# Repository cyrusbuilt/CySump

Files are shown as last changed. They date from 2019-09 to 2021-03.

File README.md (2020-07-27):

# CySump



ESP8266-based automated IoT sump pump system (Arduino).

The code in this repository represents the Firmware for the CySump IoT sump pump controller device, as well as some components for integrating with [OpenHAB2](https://openhab.org).  CySump is a [PlatformIO](https://platformio.org/) project and is meant to integrate with an existing sump pump and provide 2 things: The ability to detect state (the system's state, pump state, and pit state {water level}) and the ability to control the pump MQTT. Since there is an [ESP8266](https://www.adafruit.com/product/2471) at the heart of it, that means it is WiFi-enabled and is capable of OTA (Over-the-Air) firmware updates.

## Important Note on Security

CySump uses [MQTT](http://mqtt.org/) to pass control messages in JSON format and in turn the device sends status messages in JSON format to MQTT subscribers (such as OpenHAB2). Additionally, these messages are transferred to/from MQTT over TLS using SSL certificates so that the messages are encrypted (when TLS is enabled).  You cannot send control messages to CySump directly. You have to publish them to the control channel on the MQTT broker that CySump is subscribed to. Additionally, you would need the appropriate certificate and SHA256 fingerprint (when TLS is enabled) to connect to and publish the control messages. This security architecture is certainly not infalible, but definitely adds a strong layer of security that was non-existent in previous versions and also provides some means of hardening that security even further (such as using certificates signed by an RSA CA (as opposed to self-signed certs) and using password authentication with the MQTT broker on top of that. You can even configure OpenHAB2 to communicate with the MQTT broker using TLS as well, although this is overkill if the broker is running on the same machine as OpenHAB2 and/or the MQTT standard port is bound to the OpenHAB2 host).

## Theory of Operation

The way this is intended to work is: when the device detects the water level in the pit is at a certain level (at least 40% full by default), it turns on the pump via a relay and when the water level drops back down to at least 5% (by default) it shuts the pump off. If for some reason, the water level reaches roughly 83% full (about 5 inches from the water surface to the top of the pit), then the piezo buzzer will turn on and will not turn back off until the water drops below the alarm threshold. If using the OpenHab2 components, then a push notification will be sent when the water level reaches roughly 80% full and then again if the pit actually floods. The idea is not only to be able to control the pump, but alert the user to critical water level and flood conditions. Ideally, this detection and alert mechanism could be used to minimize or prevent damage.  Water level detection is performed using a special type of capacitive fluid level sensor called an "[eTape](https://www.whiteboxes.ch/shop/etape/)". Since my sump pit is roughly 30", I purchased the 32" (81.28cm) eTape.  There is a library in the [ArduinoHAF](https://platformio.org/lib/show/1185/ArduinoHAF) framework (which is a dependency) called "WaterLevelSensor" which does the heavy lifting. It samples the sensor value, converts to resistance, then converts to percentage
full and fluid depth level.  Previous versions of CySump used an HC-SR04T (and later a JSN-SR04T, which is waterproof) ultrasonic ranging sensor, which sounded like a good idea in theory, but in practice it was just to erratic and unreliable.  The sump pit itself created too much back-scatter for the sensor and on multiple occasions, the water level was higher than reported and the alarm did not sound in time.  The eTape has been ultra-reliable so far, though much more expensive.

## Configuration

The config.h file contains default configuration directives. These options are the hardcoded default values that the system will initially boot with. However, if there is a config.json file present in the root of the SPIFFS file system, then it will override these defaults. Here we'll discuss each option:

- ENABLE_OTA: If you do not wish to support OTA updates, just comment this define.
- ENABLE_MDNS: If you do not wish to support [MDNS](https://tttapa.github.io/ESP8266/Chap08%20-%20mDNS.html), comment this define.
- ENABLE_TLS: If you wish to use TLS support (MQTT-over-SSL), uncomment this define.
- PIT_DEPTH_INCHES: The depth of the pit in inches. Or more importantly, the distance between the sensor and the bottom of the sump pit. Default is 30.
- ALARM_DEPTH_INCES: This is the *remaining* depth to consider the sump pit to be critical. This is the distance (in inches) from the sensor to the water surface. Default is 5 inches (remaining before flooding).
- CONFIG_FILE_PATH: This is the path to the configuration file. The default is /config.json. The values in this file will override these defaults.
- DEFAULT_SSID: Change this line to reflect the SSID of your WiFi network.
- DEFAULT_PASSWORD: Change this line to reflect the password to your WiFi network.
- CLOCK_TIMEZONE: The GMT offset for your timezone (EST [America/New York] is -4 when observing DST. It's -5 when not.)
- SERIAL_BAUD: While it is not recommended, you can change the BAUD rate of the serial port here.
- CHECK_WIFI_INTERVAL: The interval (in milliseconds) to check to make sure the device is still connected to WiFi, and if not attempt to reconnect. Default is 30 seconds.
- CHECK_SENSORS_INTERVAL: The interval (in millisceonds) to check the water depth.
- CLOCK_SYNC_INTERVAL: The interval (in milliseconds) to try to resync the clock with NTP. Default is 1 hour.
- DEVICE_NAME: This essentially serves as the host name of the device on the network.
- CHECK_MQTT_INTERVAL: The interval (in milliseconds) to check connectivity to the MQTT broker. If the connection is lost, a reconnect will occur. The default value is 35 seconds.
- MQTT_TOPIC_STATUS: The MQTT status topic to publish device status messages to. Default is 'cysump/status'.
- MQTT_TOPIC_CONTROL: The MQTT control topic to subscribe to for control messages. Default is 'cysump/control'.
- MQTT_BROKER: The hostname or IP of the MQTT broker.
- MQTT_PORT: The port on the MQTT broker to connect to. The default is 8883 (default port for MQTT over TLS).
- OTA_HOST_PORT: Defines the port to listen for OTA updates on. This option is ignored if ENABLE_OTA is disabled.
- OTA_PASSWORD: The password used to authenticate with the OTA server. This option is ignored if ENABLE_OTA is disabled.
- ip: The default IP address. By default, this devices boots with a static IP configuration. The default IP is 192.168.0.202. You can change that here if you wish.
- gw: The default gateway address. The current default is 192.168.0.1. You can change that here if you wish.
- sm: The subnet mask. By default, it is 255.255.255.0, but you can change that here if need be.

To override the default configuration options, you need to upload a filesystem image containing a file named 'config.json' in the root of the SPIFFS filesystem. The file should like something like this:

```json
{
    "hostname": "CYSUMP",
    "useDHCP": false,
    "ip": "192.168.0.202",
    "gateway": "192.168.0.1",
    "subnetMask": "255.255.255.0",
    "dnsServer": "192.168.0.1",
    "wifiSSID": "your_ssid_here",
    "wifiPassword": "your_password_here",
    "webserverPort": 80,
    "otaPort": 8266,
    "otaPassword": "your_ota_password_here",
    "mqttBroker": "your_mqtt_broker_here",
    "mqttPort": 8883,
    "mqttControlChannel": "cysump/control",
    "mqttStatusChannel": "csump/status",
    "mqttUsername": "your_mqtt_username",
    "mqttPassword": "your_mqtt_password",
    "serverFingerprintPath": "/mqtt.fpn",
    "caCertificatePath": "/ca.crt",
    "pitDepth": 30,
    "activatePercentFull": 65,
    "deactivatePercent": 15
}
```

This configuration file is pretty self explanatory and one is included in the source. The file *MUST* be located in the "data" directory located in the root of the project in order to be picked up by the flash uploader (either via Serial or OTA). Each of the options in the configuration file are self-explanatory and match up with the hard-coded default settings mentioned above. If this file is not present when the firmware boots, a new file will be created and populated with the hardcoded defaults. These defaults can then be changed via the fail-safe menu and saved. You'll notice a couple of additional options in the config.json file not present in config.h. They are as follows:

- mqttUsername: If you have enabled password authentication on your MQTT broker, provide the username here.
- mqttPassword: If you have enabled password authentication on your MQTT broker, provide the password for the username above. If *both* the username and password are provided, then CyGarage will attempt to connect to the broker with the provided credentials; Otherwise, it will attempt to connect without credentials.
- mqttControlChannel: The MQTT control topic to subscribe to in order to receive device commands.
- mqttStatusChannel: The MQTT status topic to publish device status to.
- serverFingerprintPath: The path to the file containing the MQTT broker's SHA256 fingerprint. Default is '/mqtt.fpn'.
- caCertificatePath: The path to the CA certificate that the MQTT broker's certificate was signed with. Default is '/ca.crt'.

If the above values are omitted or invalid, then the system will fail during loadCertificates() and will not be able to connect to MQTT.  However, if ENABLE_TLS is commented out, they will be ignored and the system will attempt to connect to the MQTT broker without TLS.

## Getting Started

After you've configured everything the way you need it (as discussed above), build the firmware by either clicking "Build" in the PlatformIO tasks menu, or by opening a terminal to the project directory and typing:

```bash
> platformio run
```

NOTE: The first time you flash the Huzzah, you need to do so over serial (since the OTA code isn't there yet), but subsequent uploads can be done via OTA if configured properly.

The next thing to do is connect the Huzzah to your computer using an FTDI cable like [this one](https://www.adafruit.com/product/70?gclid=EAIaIQobChMIm7-50ZiZ5AIVlIvICh284QPxEAQYBCABEgJkcPD_BwE) and then configure the port in platformio.ini like so:

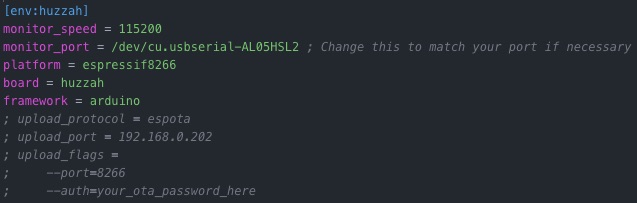
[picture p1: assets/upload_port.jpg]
config


With the above mentioned FTDI cable attached to my MacBook, the port appears as it does in the config file above (usually PlatformIO is pretty good about auto-detecting the port for you).

Now all you have to do is flash the firmware onto the Huzzah. You can do this by first pressing and holding the "GPIO" button and then press the "reset" button and let go of both on the Huzzah to put it into flash mode (this is not necessary when you flash via OTA), then click the "Upload and Monitor" task in the PlatformIO menu or by typing the following into the terminal:

```bash
> platformio run --target upload
> platformio device monitor --baud 115200 --port /dev/cu.usbserial-AL05HSL2
```

Once complete, press the "reset" button on the Huzzah. You should see the device boot up in the serial console. Now put the device back into flash mode. If you are using MQTT over TLS (recommended) then visit the readme in the "openhab" folder (even if you ultimately are not connecting MQTT to OpenHAB) for instructions on generating the necessary files for connecting CySump to MQTT, otherwise just click the "Upload File System Image" task in the PlatformIO menu. When finished, press the "reset" button again and the device will reboot and come back up with your new configuration settings.

## OTA Updates

If you wish to be able to upload firmware updates Over-the-Air, then besides leaving the ENABLE_OTA option uncommented, you will also need to uncomment all the upload_* lines in platformio.ini, and change the line 'upload_port = ' line to reflect the IP of the device and the line '--auth=' to reflect whatever OTA_PASSWORD is set to. Then when you click "upload" from the PlatformIO tasks (or if you execute 'platformio run --target upload' from the command line) it should upload directly over WiFi and once completed, the device will automatically flash itself and reboot with the new version. If you wish to upload a new configuration file, you can also do this via OTA. Assuming the above-mentioned settings are configured, you can then click "Upload File System Image" from the PlatformIO project tasks.

## Serial Console Menu

If the device ever fails to connect to WiFi or if you press the 'I' key on your keyboard while in the serial console, normal operation of the device is suspended and the device will fall into a 'fail-safe' mode and present the user with a command menu. Here we will discuss those menu options:

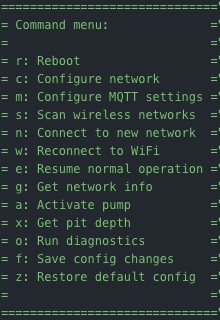
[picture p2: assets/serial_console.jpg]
Console Menu


- Activate Pump - Press 'a'. Activates the pump and ignores inputs until the user stops the pump.
- Reboot - Press 'r'. Self-explanatory. Reboots the device.
- Configure pit depth - Press 'l'. Configure the depth of the sump pit.
- Configure network - Press 'c'. Configure the network.

- - Press 'd' for DHCP or 't' for static IP.

- - If static, then you will also be prompted for the IP, gateway, DNS, and subnet mask.

- Configure MQTT settings - press 'm'. You will be prompted for broker hostname/IP and port, control and status topics, and authentication credentials.

- Scan wireless networks - Press 's'. This will scan for available wireless networks and dump a table of the networks it found to the console.

- Connect to new network - Press 'n'. This option prompts the user for a new SSID and password for different WiFi network to connect to.

- Reconnect to WiFi - Press 'w'. This can be used to reconnect to the current WiFi network if the connection was lost.

- Resume normal operation - Press 'e'. This will leave fail-safe mode and attempt to resume normal operation by resuming any suspended tasks and verify network connectivity.

- Get network info - Press 'g'. This will dump network information to the serial console (IP config, WiFi connection info).

- Run diagnostics - Press 'o'. This will run system diagnostics (similar to POST) to verify critifcal system functions are working correctly.

- Report pit depth - Press 'x'. This lets you get the current depth reading (without triggering any alarm states). Useful for determining the actual depth for configuration.

- Enable alarm - Press 'q'. This enables the audible alarm if disabled.

- Disable alarm - Press 'u'. This disables the audible alarm until manually enabled again.

- Save config changes - Press 'f'. This will save any configuration changes currently stored in memory to config.json.

- Restore default config - Press 'z'. This will restore the firmware configuration back to the factory default settings (the hard-coded defaults). It does this by simply deleting the existing config.json file from flash storage and then immediately rebooting the firmware. Upon reboot, a new config.json file is created and populated with the default settings which are then applied to the running configuration in memory.

## Dependencies

The firmware dependencies will be installed automatically at compile-time.  However, if you wish to install dependencies prior to compiling (for intellisense or to clear warnings/errors in the VSCode editor) you can run the following command:

```bash
> platformio lib install
```

Then go to the platformio menu and click "Rebuild IntelliSense index".

## Tools

Included with this firmware is a few handy tools:

- /disassemble.sh - Disassembles the compiled firmware into a plain text file called 'disassembly.txt'. If the firmware has not been built, it will be compiled first, then disassembled. The disassembly output contains the assembly code, C++ calls, and instruction addresses useful for debugging the executing code or determining the cause of crashes at addresses reported by ESPCrashMonitor during boot.

- tools/clear_flash.sh - Completely clears the flash memory on the ESP8266 of all data (including firmware).

- tools/serial_monitor.sh - Just runs the serial monitor. Pretty much the same as clicking 'Monitor' in the platformio menu, but uses its own settings instead of those found in platformio.ini.

- tools/generate_mqtt_certs.sh - Generates the necessary certificates for the MQTT broker and CySump to communicate over TLS.

## Integration with sump pump

Once the board is assembled (either by having the board etched or by just soldering the necessary components to perf board and making the connections manually), you will need to mount the board somewhere and then make the necessary connections to the pump. To do this involves working with high-voltage. *BE CAREFUL DAMNIT*. I am not liable if you do something wrong and injure yourself or blow up your pump. Ok?? Are we clear on this??

Good. I hope so.

For those of you that have done this sort of thing before, this should be trivial. If you don't have any experience with this stuff, please consider having an electrician do the work or at least someone with experience.  The best approach is *NOT* to modify the power cord on your pump. My best recommendation would be to use a 3-pronged extension cord, cut it in half and then splice the ground and neutral wires back together but leave at lest a few inches of wire out of the outer sheath. When you splice those wires, use something heavy duty (good wire nuts, solder and shrink tube, or maybe good crimp-on connectors rated for high voltage. But don't be silly and just twist them together and wrap them in electrical tape. That's just begging for trouble.

Strip both pieces of remaining 'hot' wire. Connect the 'hot' wire from the male plug to the center terminal of a 3-position toggle switch rated for at least 120VAC @ 10A. Connect the 'hot' wire of the female plug to the NO terminal on the relay. Take another wire of the same guage and connect one end to the NO terminal as well. Take the other end and connect it to one of the other terminals on the toggle switch. When the switch is in the center position, the pump is 'off' and will NOT run. When switched to whatever position that other terminal is, it will be 'manually on'. Now take another wire of the same guage and connect one end to the oposite terminal on the toggle switch and then the other end to the COM terminal on the relay. When switch to this position, the pump will be 'auto', meaning it is controlled by CySump. Ideally, all the switch and wiring will be inside of a proper electrical box with a face plate the switch mounts to. Now connect the male plug to the electrical outlet, and plug the pump into the female end. Test 'manual' mode to verify the pump turns on and nothing bad happens. DO NOT let the pump run for more than a few seconds if there is no water in the pit. You can burn out your pump.

Now you need to mount the eTape sensor. How you do this is up to you and depends on the sump pit. You *should* have a lid on the pit. The eTape should be mounted so that the top of tape is as close to the top of the pit as possible it is generally attached to the wall of the sump pit.  As the fluid level rises, the capacitance value changes. It would be worth checking pit depth from the serial console menu ('x' command) once the sensor is mounted and the pit is completely dry. This would give you a definitive baseline depth reading, not just of the depth of the pit, but more importantly, the distance from where the sensor is mounted, to the bottom of the pit. Even though the standard depth is 30 inches, usually there is some gravel or something like that at the bottom and you also have to consider exactly where the sensor is mounted, all of which affect the depth reading. Adjust the value for PIT_DEPTH_INCHES in config.h to reflect that value.  Sensor position is important!! You may need to take several readings with and without water to get a good baseline.

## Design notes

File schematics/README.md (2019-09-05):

# CySump Schematics

All files were produced using [Fritzing](https://fritzing.org/home/). The following is a list of files and what they are:

- CySump_bb.pdf - A PDF version of the breadboard view.

- CySump_bom.html - The bill of materials in HTML format.

- CySump_pcb.pdf - A PDF version of the PCB view.

- CySump_schem.pdf - A PDF version of the schematic view.

- CySump.fzz - The original Fritzing CAD file.

## NOTES

Firstly, the buzzer and the HCSR04 sensor should *NOT* be mounted to the board. Instead, pin headers should be soldered in there place and then female pin connectors should be used to connect them to the board. This may require making a cable (of sorts) for them and then the buzzer can be mounted somewhere inside whatever housing you use or somewhere external to the board. The sensor needs to be mounted somewhere at the top of the pit. Either by affixing the sensor to a bracket or board that straddles the top of the pit or affixed to the underside of the pit lid, then a cable will need to connect the sensor to the board.

The [Adafruit Power Relay FeatherWing](https://www.adafruit.com/product/3191?gclid=EAIaIQobChMIyfvxycGo4wIVTfDACh0WFg4LEAAYASAAEgL4v_D_BwE) was used because it had a 3V trigger and built-in logic-level and protection circuitry (which means no problems connecting to the ESP8266 and no additional transistors or diodes needed). This board needs to have a pin configured as the 'signal' (trigger) line. I chose pin A which is to the immediate right of the GND pin. This is done by simply soldering the jumper pads next to that pin on the underside of the board.

The power supply used is a 5VDC 1A supply which connects to J2.

NO and COM on the relay should connect to the power line that feeds the pump. This may require cutting and splicing the power cord or modifying an extension cord (the preferred option) and then plugging the pump into the extension. The idea is to use the relay as a power switch. So you want to cut and strip the "hot" wire and connect the 2 ends to the relay.  An even better implementation would be to use a 3-position DPDT Toggle switch rated for at least 120V @ 10A between the power cord and relay. When wired properly, this would allow you to switch between "manual" mode where the pump just runs when needed (or switches over to the float switch that goes with it) and "auto" mode, where CySump then controls the pump in an automated fashion. Personally, I intend to mount an electrical box with a cover plate and toggle switch near the electrical outlet the pump currently plugs into, then cut an extension cord and wire to the switch and CySump controller, with the female end of the extension hanging out so that I can plug the pump into it.

Additionally, I opted to use stacking headers where the pins of the ESP8266 should go (creating a "socket" of sorts) to allow the module to be removable. This is optional, but handy in the event that the module ever becomes damaged or if the EEPROM wears out, or something of that nature, it can be easily replaced.

Lastly, the HCSR04 sensor is NOT waterproof. This presents a problem which I will likely later be resolved with a different sensor. While, I can take some level of precautions by coating most of the module in hot glue or something like that, you cannot cover the cans as they were designed to operate in dry air with nothing in between them. Considering this sensor will be mounted at the top of the pit somewhere or even affixed to the underside of the sump pit lid, sooner or later the moist air will corrode the sensor. As such, the sensor will likely need to be replaced every so often. Since they are cheap ($4 or $5 USD), this isn't an expensive proposition, but should be resolved nonetheless. A future revision will replace this sensor with something more robust and less affected by environmental conditions.

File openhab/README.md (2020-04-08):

# OpenHAB Components

This directory contains components for integrating with OpenHAB2.

## Instructions for integrating with OpenHAB2

The first thing you will need to do if you haven't already, is install an MQTT broker. For the purposes of this guide, I will assume you will be using [Mosquitto](https://mosquitto.org/) and will be installing it on the same machine as OpenHAB2.

To install mosquitto, follow the download and install instructions [here](https://mosquitto.org/download/). But assuming you are installing on an Ubuntu or Ubuntu-based system just run:

```bash
> sudo apt-add-repository ppa:mosquitto-dev/mosquitto-ppa
> sudo apt-get update
> sudo apt install mosquitto mosquitto-clients
```

## The following instructions are only necessary when TLS is enabled

Next we need to generate the necessary SSL certificates that will be used for communication over TLS.  There is a shell script in the tools directory that simplifies this process. Just run:

```bash
> tools/./generate_mqtt_certs.sh
```

You will first be prompted for the hostname and IP address of your MQTT broker (in this example, it is the same as the your OpenHAB2 server). It will also prompt you for some additional information such as country, state/province, Organizational Unit, org name, etc. It will also prompt you for a password. Make note of this password. When the script is finished it will output a bunch of files in tools/certs. As the script indicates, the ones we are most interested in are host_name.key.pem, hostname_.crt.pem, and ca.crt.pem (where host_name is the host name you provided when the tool first ran). These 3 files need to be copied somewhere on your MQTT server. For this example let's assume /etc/mosquitto/certs.

```bash
> sudo mkdir /etc/mosquitto/certs
> sudo cp -f tools/certs/host_name.key.pem /etc/mosquitto/certs
> sudo cp -f tools/certs/host_name.crt.pem /etc/mosquitto/certs
> sudo cp -f tools/certs/ca.crt.pem /etc/mosquitto/certs
```

## END TLS-SPECIFIC CONFIG

Next, we need to configure it.

```bash
> sudo nano /etc/mosquitto/mosquitto.conf
```

First make sure the following line is present:

```txt
listener 1883 localhost
```

This binds port 1883 (the default non-SSL port) for MQTT to only allow traffic from the local host.  This is done because encrypting the traffic between OH2 and MQTT when they are running on the same host is overkill, but we also need to make sure that *ONLY* the localhost can do this.  All other traffic will then have to go through another port. In our case, 'all other traffic' will be encrypted traffic when TLS is enabled. This means we need to define another port and supply the certificates like so:

```txt
listener 1883 localhost

listener 8883
cafile /etc/mosquitto/certs/ca.crt.pem
certfile /etc/mosquitto/certs/host_name.crt.pem
keyfile /etc/mosquitto/certs/host_name.key.pem
```

If you are *NOT* using TLS, you can simply leave all the certificate lines out of the config (or comment them). Now press CTRL+X to save and close the file.  Now restart MQTT:

```bash
> sudo systemctl restart mosquitto.service
> sudo systemctl status mosquitto.service
```

It should start back up normally and show the status as active. Now lets test it out:

```bash
> mosquitto_sub -h localhost -p 1883 -t cysump/status &
> mosquitto_pub -h localhost -p 1883 -t cysump/status -m "{\"foo\":\"bar\"}"
{"foo":"bar"}
```

You should see the message output. Now you can kill the subscription you created with the first command:

```bash
> fg
```

Now press CTRL+C.

Next, we need to configure OpenHAB to use the MQTT broker. To do this, go to PaperUI -> Addons -> Bindings and install the MQTT Binding.  Once the installation is complete, we need to configure the service:

```bash
> sudo nano /etc/openhab2/services/mqtt.cfg
```

Add the following lines:

```txt
mqtt:localBroker.url=tcp://localhost:1883
mqtt:localBroker.clientId=openhab2
mqtt:localBroker.qos=0
```

Save and close the file.

## Optional password authentication

If you wish to use password authentication with Mosquitto, then there are some additional steps. First, you need to generate the password file.

```bash
> sudo mosquitto_passwd -c /etc/mosquitto/passwd cysump
```

Where "cysump" is the username. You can make this whatever you want as long as this same username is what you put in the CySump config and in the mqttbridge.things file (if you don't already have an existing bridge). Next, we need to modify the mosquitto config again:

```bash
> sudo nano /etc/mosquitto/mosquitto.conf
```

And add the following lines to the file:

```txt
allow_anonymous false
password_file /etc/mosquitto/passwd
```

Save and close, then restart the service:

```bash
> sudo systemctl restart mosquitto.service
```

Next we need to copy the following files to the openhab-conf folder on the server:

## rrd4j.persist

This is a persistence configuration file. This is only needed if you are using RRD4J for the persistence engine in OpenHAB2 and don't already have a persistence file for it (althouh the settings in this file are recommended). NOTE: Peristence is required to make use of historical water depth tracking. If you don't need this feature or are using a different persistence engine, you can ignore this file. Otherwise, copy this file to the openhab-conf/persist directory.

## mqttbridge.things

This is a "Thing" definition for the MQTT bridge. This bridge can be used by anything else in OH2 that needs it. This simply defines a bridge to MQTT that registers OH2 as a client. If a Thing definition for this bridge already exists, no need to copy it again. If not, then copy this file to the openhab-conf/things directory.

## cysump.things

This is a "Thing" definition for CySump that binds the channels we need to MQTT.  You can edit the binding if needed, (such as adding the mosquitto username and password, hostname or IP and port) then copy this file to the openhab-conf/things directory.

## cysump.items

This file defines the items that will bind to the channels in the cysump.things file, which will represent controls and display values. Copy this file to your openhab-conf/items folder.

## cysump.sitemap

This is the sitemap contains all the items defined in the cysump.items file and makes up all the monitor and control items on one screen. Copy this file to your openhab-conf/sitemaps folder.

## cysump.rules

Contains automation logic. This file is responsible for sending push notifications if the pit is getting too full or if it has flooded, and handles the control actions. Copy this file to your openhab-conf/rules folder.

## All set

Now that everything is in place. You need to restart OH2:

```bash
> sudo systemctl restart openhab2.service
```

Now lets make sure the service started successfully:

```bash
> sudo systemctl status openhab2.service
```

The service should be active. So let's test it:

```bash
> mosquitto_pub -h localhost -p 1883 -t cysump/status -m "{\"client_id\":\"test\",\"pumpState\":\"OFF\",\"firmwareVersion\":\"1.0\",\"systemState\":0,\"waterLevelPercent\":50,\"waterDepth\":12,\"pitState\":\"LOW\",\"alarmEnabled\":true}"
```

Now if you navigate to BasicUI in OH2 and click the CySump sitemap, you should see the System ID is "test", Firmware version is "1.0", System State is "Booting 0" and Pump state is "OFF".

CySump Sitemap (Web Version)

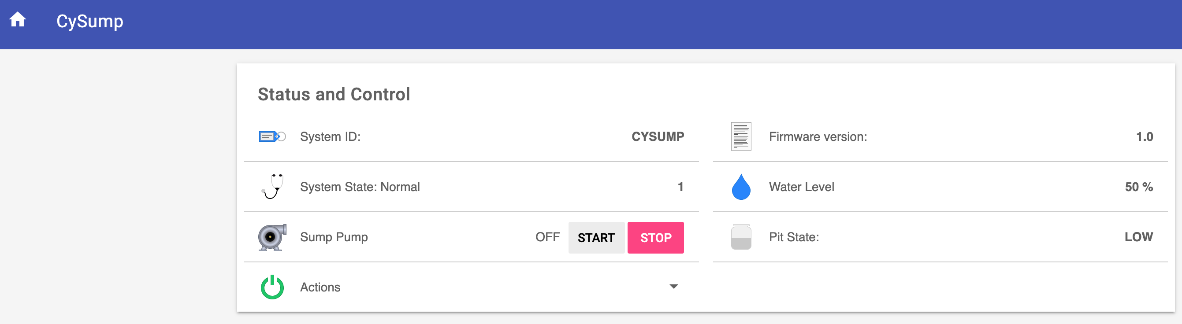
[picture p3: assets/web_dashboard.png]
Web Dashboard


CySump Sitemap (OH2 Mobile App Version)

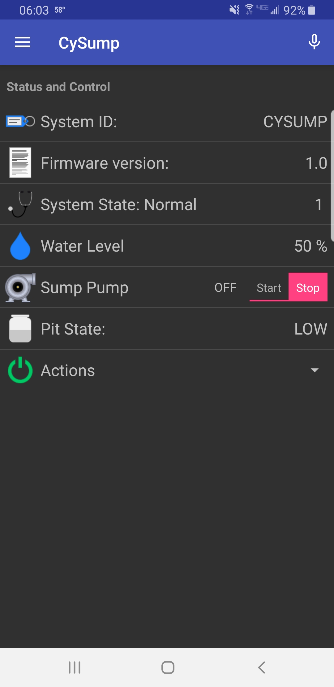
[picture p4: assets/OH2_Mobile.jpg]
Mobile Dashboard


## Dependencies

You will need the following dependent add-ons installed in OpenHAB2 for these components to work correctly:

[openHAB Cloud Connector](https://www.openhab.org/addons/integrations/openhabcloud/)

- You also need to connect your local OpenHAB server to a cloud instance in order to receive push notifications.

This is because cysump.rules makes use of the sendBroadcastNotification() method which assumes you have linked your local OH2 server to a cloud OH2 instance, which can then make use of push notifications. If you do not wish to use push notifications or just don't want to link your local installation to a secure cloud instance, then don't install the cloud connector and comment out the necessary line cysump.rules.

[RRD4J Peristence add-on](https://www.openhab.org/addons/persistence/rrd4j/)

- Required for historical water depth graphs if no other persistence engine is being used.

If all went well, you can now use CySump with your OH2 installation and control and monitor the sump pump (securely) using the OH2 web console or via the OH2 mobile app.

## Finishing up

At this point the only thing left to do if you haven't already is to compile and upload the firmware (if you are happy with the defaults in config.h and your settings in config.json). Next make sure the device is operating normally and you can ping the IP of the device. You can even publish a command to the device to force it to report it's status back:

```bash
> mosquitto_pub -h localhost -p 1883 -t cysump/control -m "{\"client_id\":\"CYSUMP\",\"command\": 4}"
```

The 'data' directory in this project should now contain 3 files: config.json, ca.crt, and mqtt.fpn.

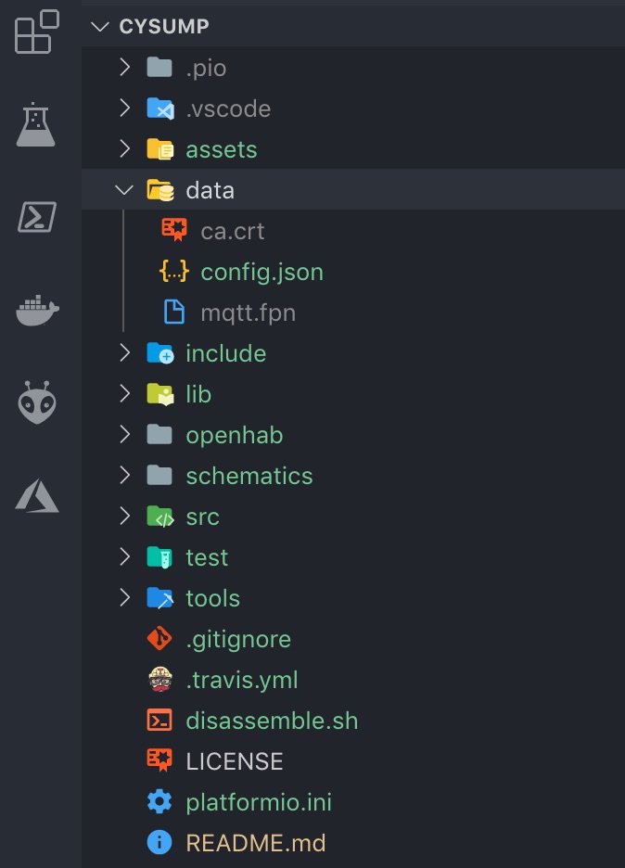
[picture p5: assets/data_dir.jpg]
Data Folder


If so, click "Upload File System image" from the PlatformIO tasks and it will upload those files to CySump and it will reboot when finished. Once it comes back up, it should be able to establish a connection to MQTT and you should see it's status in OH2.

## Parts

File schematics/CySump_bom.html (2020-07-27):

Label | Part Type | Properties
Huzzah ESP8266 | Adafruit HUZZAH ESP8266 | variant variant 2; part # Adafruit #2471
J1 | Piezo Speaker
J2 | Screw terminal - 2 pins | package THT; pins 2; hole size 1.0mm,0.508mm; pin spacing 0.1in (2.54mm)
J3 | Generic male header - 3 pins | row single; package THT; hole size 1.0mm,0.508mm; pins 3; form ♂ (male); pin spacing 0.1in (2.54mm)
LED1 | Green (570nm) LED | package 5 mm [THT]; color Green (570nm); leg yes
LED2 | Red (633nm) LED | package 5 mm [THT]; color Red (633nm); leg yes
LED3 | Yellow (595nm) LED | package 5 mm [THT]; color Yellow (595nm); leg yes
Part1 | Schematic Frame | descr Automated IoT Sump Pump Controller; sheet 1/1; filename CySump.fzz; date 1571939862; project CySump Controller; rev 1.5
Power Relay Featherwing | Adafruit PowerRelay Feather Wing | variant variant 1; part # Adafruit #3191
R1 | 560Ω Resistor | bands 4; package THT; tolerance ±5%; pin spacing 400 mil; resistance 560Ω
S1 | SPST Switch | package switche-dpdt; variant pth2
Amount | Part Type | Properties
1 | Adafruit HUZZAH ESP8266 | variant variant 2; part # Adafruit #2471
1 | Piezo Speaker
1 | Screw terminal - 2 pins | package THT; pins 2; hole size 1.0mm,0.508mm; pin spacing 0.1in (2.54mm)
1 | Generic male header - 3 pins | row single; package THT; hole size 1.0mm,0.508mm; pins 3; form ♂ (male); pin spacing 0.1in (2.54mm)
1 | Green (570nm) LED | package 5 mm [THT]; color Green (570nm); leg yes
1 | Red (633nm) LED | package 5 mm [THT]; color Red (633nm); leg yes
1 | Yellow (595nm) LED | package 5 mm [THT]; color Yellow (595nm); leg yes
1 | Schematic Frame | descr Automated IoT Sump Pump Controller; sheet 1/1; filename CySump.fzz; date 1571939862; project CySump Controller; rev 1.5
1 | Adafruit PowerRelay Feather Wing | variant variant 1; part # Adafruit #3191
1 | 560Ω Resistor | bands 4; package THT; tolerance ±5%; pin spacing 400 mil; resistance 560Ω
1 | SPST Switch | package switche-dpdt; variant pth2

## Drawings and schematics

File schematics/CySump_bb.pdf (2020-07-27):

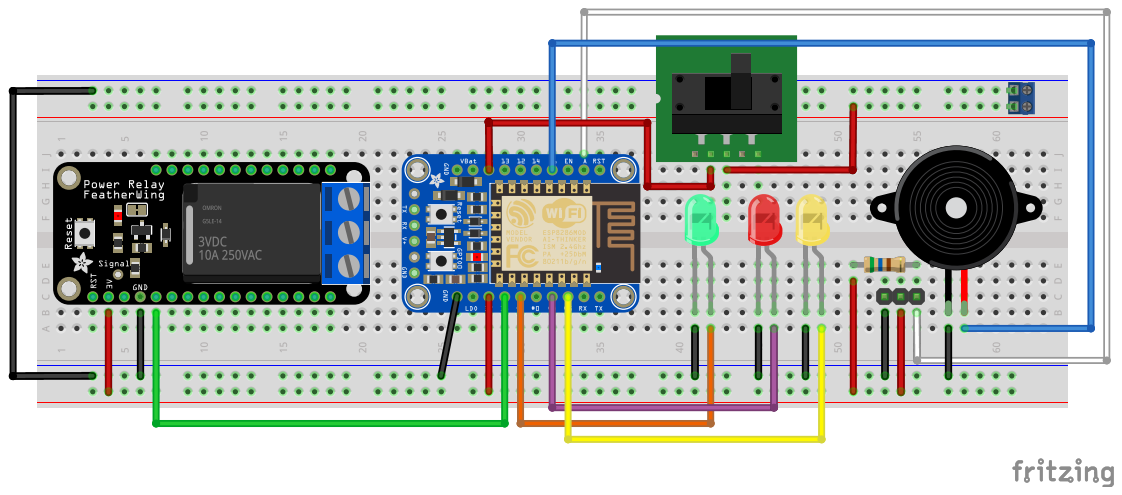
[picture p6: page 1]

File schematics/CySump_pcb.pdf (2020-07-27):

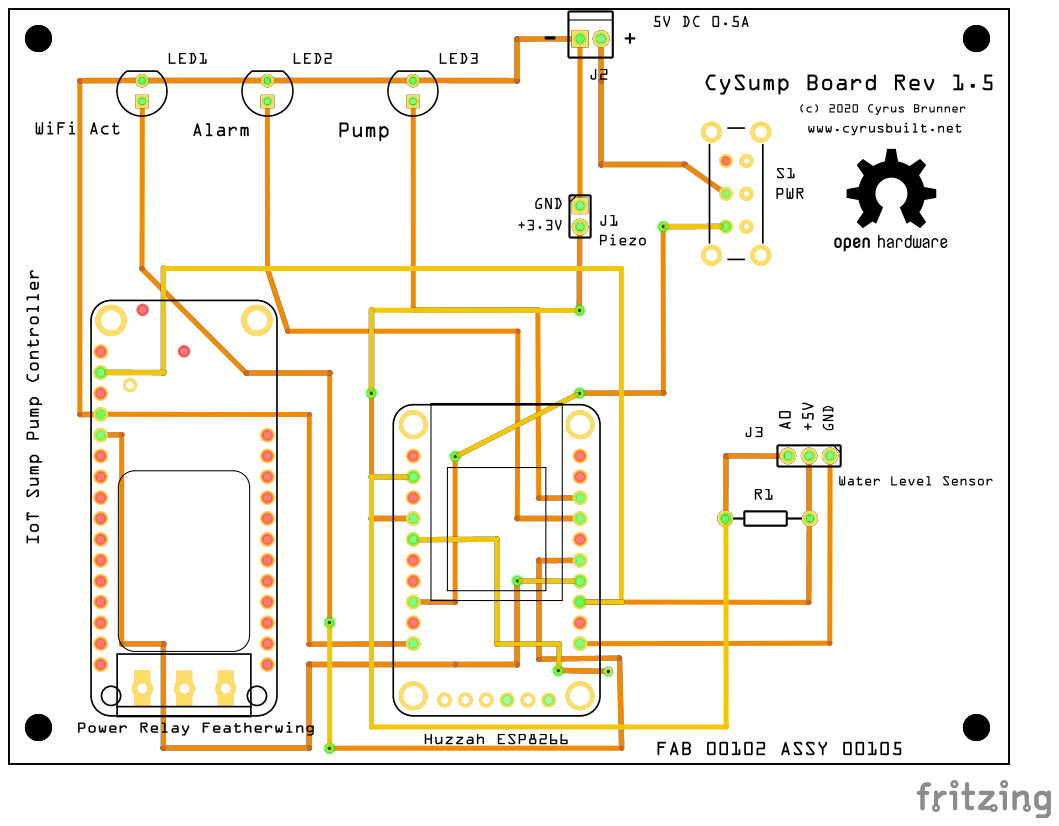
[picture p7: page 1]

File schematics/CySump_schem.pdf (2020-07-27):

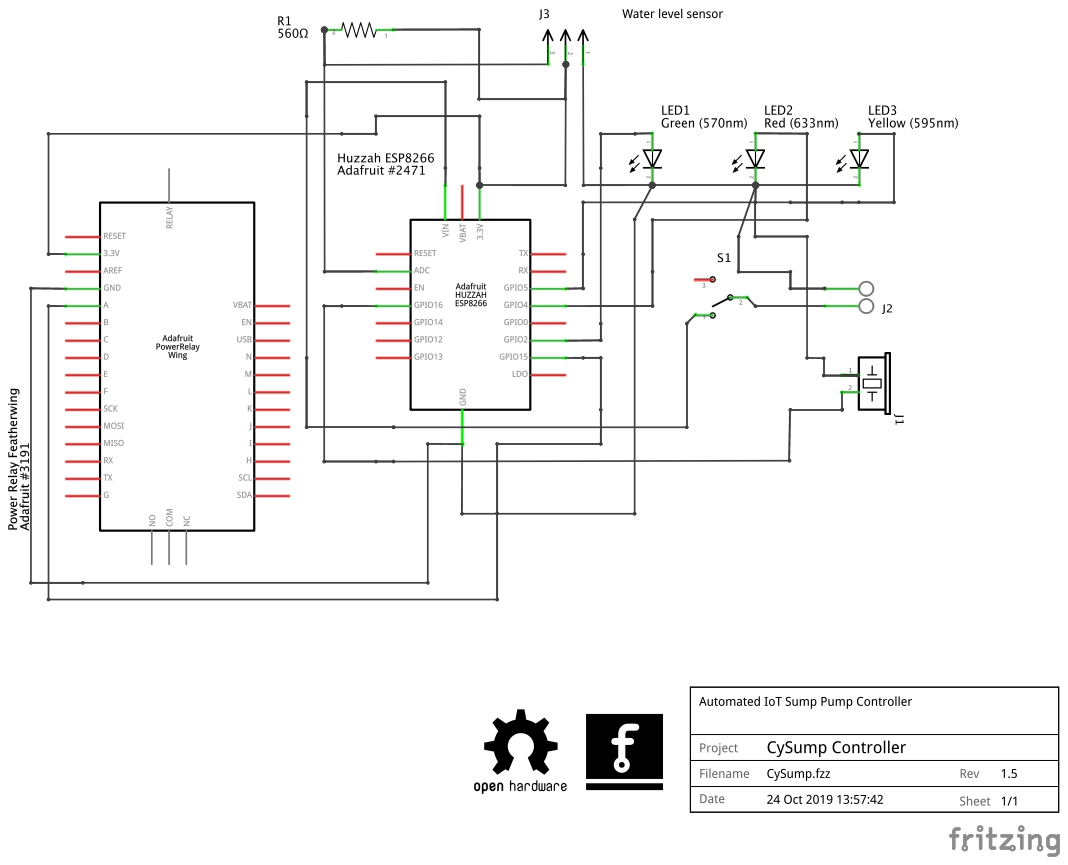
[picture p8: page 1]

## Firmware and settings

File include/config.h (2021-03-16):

/**
 * System Configuration defaults. These values will be used at boot time
 * if no overriding configuration is present.
 */

#ifndef config_h
#define config_h

#include <IPAddress.h>

// Configuration
#define ENABLE_OTA                              // Comment this line to disable OTA updates.
#define ENABLE_MDNS                             // Comment this line to disable the MDNS.
#define PIT_DEPTH_INCHES 32                     // The depth of the sump pit (inches).
#define ALARM_DEPTH_INCHES 5                    // The depth at which to consider an alarm state (inches left until full)
#define CONFIG_FILE_PATH "/config.json"         // The config file path. Do not alter unless you are sure.
#define DEFAULT_SSID "your_ssid_here"           // Put the SSID of your WiFi here.
#define DEFAULT_PASSWORD "your_password_here"   // Put your WiFi password here.
#define CLOCK_TIMEZONE -4                       // The timezone this device is located in. (For example, EST when observing DST = GMT-4, when not = GMT-5)
#define SERIAL_BAUD 115200                      // The BAUD rate (speed) of the serial port (console).
#define CHECK_WIFI_INTERVAL 30000               // How often to check WiFi status (milliseconds).
#define CHECK_SENSORS_INTERVAL 2000             // How often to check sensors (milliseconds).
#define CLOCK_SYNC_INTERVAL 3600000             // How often to sync the local clock with NTP (milliseconds).
#define DEVICE_NAME "CYSUMP"                    // The device name.
#define CHECK_MQTT_INTERVAL 35000               // MQTT connectivity check interval (milliseconds).
#define MQTT_TOPIC_STATUS "cysump/status"       // MQTT status channel to publish to.
#define MQTT_TOPIC_CONTROL "cysump/control"     // MQTT control channel to subscribe to.
#define MQTT_BROKER "your_mqtt_broker_here"     // MQTT broker hostname or IP.
#define MQTT_PORT 8883                          // MQTT port number.
#define DEFAULT_PUMP_ACTIVATE_PERCENT 70        // Default percentage of the sump pit is full before activating the pump.
#define DEFAULT_PUMP_DEACTIVATE_PERCENT 15      // Default percentage of the sump pit is full before deactivating the pump if active.
#ifdef ENABLE_OTA
    #include <ArduinoOTA.h>
    #define OTA_HOST_PORT 8266                     // The OTA updater port.
    #define OTA_PASSWORD "your_ota_password_here"  // The OTA updater password.
#endif
IPAddress defaultIp(192, 168, 0, 202);                 // The default static host IP.
IPAddress defaultGw(192, 168, 0, 1);                   // The default static gateway IP.
IPAddress defaultSm(255, 255, 255, 0);                 // The default static subnet mask.
IPAddress defaultDns(defaultGw);                              // The default static DNS server IP (same as gateway for most residential setups)

typedef struct {
    // Network stuff
    String hostname;
    String ssid;
    String password;
    IPAddress ip;
    IPAddress gw;
    IPAddress sm;
    IPAddress dns;
    bool useDhcp;

    uint8_t clockTimezone;

    // MQTT stuff
    String mqttTopicStatus;
    String mqttTopicControl;
    String mqttBroker;
    String mqttUsername;
    String mqttPassword;
    uint16_t mqttPort;

    // OTA stuff
    uint16_t otaPort;
    String otaPassword;

    // Thresholds
    uint8_t pitDepth;
    uint8_t pumpActivatePercent;
    uint8_t pumpDeactivatePercent;
    uint8_t alarmDepthInches;
} config_t;

#endif

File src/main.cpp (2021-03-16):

/**
 * CySump
 * v1.6
 * 
 * Author:
 *  Cyrus Brunner <cyrusbuilt at gmail dot com>
 * 
 * This is the firmware for the CySump IoT Sump Pump Controller. This firmware
 * specifically targets the Adafruit Huzzah ESP8266, but could easily be
 * adapted to work on any ESP8266 MCU.  It should be relatively easy to adapt
 * to work on ESP32 modules as well, although there would need to be some
 * dependency changes.
 */

// TODO Implement FS checks in self-diags

#ifndef ESP8266
    #error This firmware is only compatible with ESP8266 controllers.
#endif
#include <Arduino.h>
#include <ESP8266WiFi.h>
#include "config.h"
#include <WiFiClient.h>
#include <FS.h>
#include <time.h>
#include "Buzzer.h"
#include "LED.h"
#include "Relay.h"
#include "TaskScheduler.h"
#include "ResetManager.h"
#include "ESPCrashMonitor-master/ESPCrashMonitor.h"
#include "ArduinoJson.h"
#include "ESP8266Ping.h"
#include "PubSubClient.h"
#include "TelemetryHelper.h"
#include "WaterLevelSensor.h"
#include "Console.h"

#define FIRMWARE_VERSION "1.6"

// Pin definitions
#define PIN_WIFI_LED 2
#define PIN_ALARM_LED 4
#define PIN_PUMP_LED 5
#define PIN_RELAY 15
#define PIN_BUZZER 16
#define PIN_LEVEL_SENSOR A0

// Forward declarations
void onRelayStateChange(RelayInfo* sender);
void onCheckWiFi();
void failSafe();
void onCheckMqtt();
void onCheckSensors();
void onMqttMessage(char* topic, byte* payload, unsigned int length);
void onSyncClock();

// Global vars
#ifdef ENABLE_MDNS
    #include <ESP8266mDNS.h>
    MDNSResponder mdns;
#endif
WiFiClient wifiClient;
PubSubClient mqttClient(wifiClient);
WaterLevelSensor sensor(PIN_LEVEL_SENSOR);
Relay pumpRelay(PIN_RELAY, onRelayStateChange, "SUMP_PUMP");
LED alarmLED(PIN_ALARM_LED, NULL);
LED wifiLED(PIN_WIFI_LED, NULL);
LED pumpLED(PIN_PUMP_LED, NULL);
Buzzer alarmBuzzer(PIN_BUZZER, NULL, "AlarmBuzzer");
Task tCheckWifi(CHECK_WIFI_INTERVAL, TASK_FOREVER, &onCheckWiFi);
Task tCheckMqtt(CHECK_MQTT_INTERVAL, TASK_FOREVER, &onCheckMqtt);
Task tSyncClock(CLOCK_SYNC_INTERVAL, TASK_FOREVER, &onSyncClock);
Task tCheckSensors(CHECK_SENSORS_INTERVAL, TASK_FOREVER, &onCheckSensors);
Scheduler taskMan;
config_t config;
float lastDepth = 0;
volatile int percentFull = 0;
bool filesystemMounted = false;
bool manualPumpMode = false;
volatile SystemState sysState = SystemState::BOOTING;
bool alarmDisabled = false;

// TODO Maybe add some logic to measure how fast the water level is rising.
// If rising too fast, especially while the pump is running, this could be
// another alarm condition. Or even more importantly, if the pump is NOT
// running when we expect it to be, that would also be a cause for concern.
// However, I'm not sure how to test that other than to see if the water
// level goes down during pump operation. If it doesn't, then either the
// pump is NOT actually running, or again... the pit is filling faster
// than we can pump. This is a highly unlikely scenario though. You would
// have to have a pretty MAJOR flood problem if the water pump is not able
// to keep up with the incoming water. More than likely, this would simply
// indicate pump failure.


/**
 * Get and print the pump status.
 * @return The pump status ("OFF" or "ON")
 */
String pumpStatus() {
    String state = "OFF";
    if (pumpRelay.isClosed()) {
        state = "ON";
    }

    Serial.print(F("INFO: Pump status = "));
    Serial.println(state);
    return state;
}

/**
 * Gets the pit state based on the specified water level percentage.
 * @param percentFull The percentage of the pit that is full of water.
 * @return 
 */
String pitState(int percentFull) {
    String state = "UNKNOWN";
    if (percentFull == 0) {
        state = "EMPTY";
    }
    else if (percentFull <= 50) {
        state = "LOW";
    }
    else if (percentFull > 50 && percentFull < 75) {
        state = "WARN";
    }
    else if (percentFull >= 75 && percentFull < 99) {
        state = "CRITICAL";
    }
    else if (percentFull >= 99) {
        state = "FLOOD";
    }

    Serial.print(F("INFO: *** Pit state: "));
    Serial.println(state);
    return state;
}

/**
 * Publishes the system state to the MQTT status channel and
 * blinks the WiFi status LED.
 */
void publishSystemState() {
    if (mqttClient.connected()) {
        wifiLED.on();

        uint16_t freeMem = ESP.getMaxFreeBlockSize() - 512;

        DynamicJsonDocument doc(freeMem);
        doc["client_id"] = config.hostname;
        doc["pumpState"] = pumpStatus();
        doc["firmwareVersion"] = FIRMWARE_VERSION;
        doc["systemState"] = (uint8_t)sysState;
        doc["waterLevelPercent"] = percentFull;
        doc["pitState"] = pitState(percentFull);
        doc["waterDepth"] = lastDepth;
        doc["alarmEnabled"] = alarmDisabled ? "OFF" : "ON";
        doc.shrinkToFit();

        String jsonStr;
        size_t len = serializeJson(doc, jsonStr);
        Serial.print(F("INFO: Publishing system state: "));
        Serial.println(jsonStr);
        if (!mqttClient.publish(config.mqttTopicStatus.c_str(), jsonStr.c_str(), len)) {
            Serial.println(F("ERROR: Failed to publish message."));
        }

        doc.clear();
        wifiLED.off();
    }
}

/**
 * Synchronize the local system clock via NTP. Note: This does not take DST
 * into account. Currently, you will have to adjust the CLOCK_TIMEZONE define
 * manually to account for DST when needed.
 */
void onSyncClock() {
    configTime(CLOCK_TIMEZONE * 3600, 0, "pool.ntp.org", "time.nist.gov");

    Serial.print("INIT: Waiting for NTP time sync...");
    delay(500);
    while (!time(nullptr)) {
        ESPCrashMonitor.iAmAlive();
        Serial.print(F("."));
        delay(500);
    }

    time_t now = time(nullptr);
    struct tm *timeinfo = localtime(&now);
    
    Serial.println(F(" DONE"));
    Serial.print(F("INFO: Current time: "));
    Serial.println(asctime(timeinfo));
}

/**
 * Handles the relay state change event. Simply changes the state of the
 * relay indicator LED.
 * @param sender The relay info.
 */
void onRelayStateChange(RelayInfo* sender) {
    if (sender->state == RelayState::RelayClosed) {
        pumpLED.on();
    }
    else {
        pumpLED.off();
    }
}

/**
 * Toggles the water pump.
 * @param run Set true to turn the pump on; false to turn it off.
 */
void togglePump(bool run) {
    if (run) {
        Serial.print(F("INFO: Activating pump @ "));
        pumpRelay.close();
    }
    else {
        Serial.print(F("INFO: Deactivating pump @ "));
        pumpRelay.open();
    }

    Serial.println(millis());
}

/**
 * Resume normal operation. This will resume any suspended tasks.
 */
void resumeNormal() {
    Serial.println(F("INFO: Resuming normal operation..."));
    taskMan.enableAll();
    wifiLED.off();
    // TODO Should we do anything with the other LEDs?
    sysState = SystemState::NORMAL;
    publishSystemState();
}

/**
 * Prints network information details to the serial console.
 */
void printNetworkInfo() {
    Serial.print(F("INFO: Local IP: "));
    Serial.println(WiFi.localIP());
    Serial.print(F("INFO: Gateway: "));
    Serial.println(WiFi.gatewayIP());
    Serial.print(F("INFO: Subnet mask: "));
    Serial.println(WiFi.subnetMask());
    Serial.print(F("INFO: DNS server: "));
    Serial.println(WiFi.dnsIP());
    Serial.print(F("INFO: MAC address: "));
    Serial.println(WiFi.macAddress());
    WiFi.printDiag(Serial);
}

/**
 * Scan for available networks and dump each discovered network to the console.
 */
void getAvailableNetworks() {
    ESPCrashMonitor.defer();
    Serial.println(F("INFO: Scanning WiFi networks..."));
    int numNetworks = WiFi.scanNetworks();
    for (int i = 0; i < numNetworks; i++) {
        Serial.print(F("ID: "));
        Serial.print(i);
        Serial.print(F("\tNetwork name: "));
        Serial.print(WiFi.SSID(i));
        Serial.print(F("\tSignal strength:"));
        Serial.println(WiFi.RSSI(i));
    }
    Serial.println(F("----------------------------------"));
}

/**
 * Reboots the MCU after a 1 second delay.
 */
void reboot() {
    Serial.println(F("INFO: Rebooting... "));
    Serial.flush();
    delay(1000);
    ResetManager.softReset();
}

/**
 * Stores the in-memory configuration to a JSON file stored in SPIFFS.
 * If the file does not yet exist, it will be created (see CONFIG_FILE_PATH).
 * Errors will be reported to the serial console if the filesystem is not
 * mounted or if the file could not be opened for writing.
 */
void saveConfiguration() {
    Serial.print(F("INFO: Saving configuration to: "));
    Serial.print(CONFIG_FILE_PATH);
    Serial.println(F(" ... "));
    if (!filesystemMounted) {
        Serial.println(F("FAIL"));
        Serial.println(F("ERROR: Filesystem not mounted."));
        return;
    }

    StaticJsonDocument<350> doc;
    doc["hostname"] = config.hostname;
    doc["useDHCP"] = config.useDhcp;
    doc["ip"] = config.ip.toString();
    doc["gateway"] = config.gw.toString();
    doc["subnetMask"] = config.sm.toString();
    doc["dnsServer"] = config.dns.toString();
    doc["wifiSSID"] = config.ssid;
    doc["wifiPassword"] = config.password;
    doc["mqttBroker"] = config.mqttBroker;
    doc["mqttPort"] = config.mqttPort;
    doc["mqttControlChannel"] = config.mqttTopicControl;
    doc["mqttStatusChannel"] = config.mqttTopicStatus;
    doc["mqttUsername"] = config.mqttUsername;
    doc["mqttPassword"] = config.mqttPassword;
    doc["activatePercentFull"] = config.pumpActivatePercent;
    doc["deactivatePercent"] = config.pumpDeactivatePercent;
    doc["pitDepth"] = config.pitDepth;
    doc["alarmDepthInches"] = config.alarmDepthInches;
    #ifdef ENABLE_OTA
        doc["otaPort"] = config.otaPort;
        doc["otaPassword"] = config.otaPassword;
    #endif

    File configFile = SPIFFS.open(CONFIG_FILE_PATH, "w");
    if (!configFile) {
        Serial.println(F("FAIL"));
        Serial.println(F("ERROR: Failed to open config file for writing."));
        doc.clear();
        return;
    }

    serializeJsonPretty(doc, configFile);
    doc.clear();
    configFile.flush();
    configFile.close();
    Serial.println(F("DONE"));
}

void setConfigurationDefaults() {
    String chipId = String(ESP.getChipId(), HEX);
    String defHostname = String(DEVICE_NAME) + "_" + chipId;

    config.hostname = defHostname;
    config.ip = defaultIp;
    config.mqttBroker = MQTT_BROKER;
    config.mqttPassword = "";
    config.mqttPort = MQTT_PORT;
    config.mqttTopicControl = MQTT_TOPIC_CONTROL;
    config.mqttTopicStatus = MQTT_TOPIC_STATUS;
    config.mqttUsername = "";
    config.password = DEFAULT_PASSWORD;
    config.sm = defaultSm;
    config.ssid = DEFAULT_SSID;
    config.useDhcp = false;
    config.clockTimezone = CLOCK_TIMEZONE;
    config.dns = defaultDns;
    config.gw = defaultGw;
    config.pitDepth = PIT_DEPTH_INCHES;
    config.pumpActivatePercent = DEFAULT_PUMP_ACTIVATE_PERCENT;
    config.pumpDeactivatePercent = DEFAULT_PUMP_DEACTIVATE_PERCENT;
    config.alarmDepthInches = ALARM_DEPTH_INCHES;
    #ifdef ENABLE_OTA
        config.otaPassword = OTA_PASSWORD;
        config.otaPort = OTA_HOST_PORT;
    #endif
}

void printWarningAndContinue(const __FlashStringHelper *message) {
    Serial.println();
    Serial.println(message);
    Serial.print(F("INFO: Continuing... "));
}

/**
 * Loads the configuration from CONFIG_FILE_PATH into memory and uses that as
 * the running configuration. Will report errors to the serial console and
 * revert to the default configuration under the following conditions:
 * 1) The filesystem is not mounted.
 * 2) The config file does not exist in SPIFFS. In this case a new file
 * will be created and populated with the default configuration.
 * 3) The config file exists, but could not be opened for reading.
 * 4) The config file is too big ( > 1MB).
 * 5) The config file could not be deserialized to a JSON structure.
 */
void loadConfiguration() {
    memset(&config, 0, sizeof(config));

    Serial.print(F("INFO: Loading config file: "));
    Serial.print(CONFIG_FILE_PATH);
    Serial.print(F(" ... "));
    if (!filesystemMounted) {
        Serial.println(F("FAIL"));
        Serial.println(F("ERROR: Filesystem not mounted."));
        return;
    }

    if (!SPIFFS.exists(CONFIG_FILE_PATH)) {
        Serial.println(F("FAIL"));
        Serial.println(F("WARN: Config file does not exist. Creating with default config..."));
        saveConfiguration();
        return;
    }

    File configFile = SPIFFS.open(CONFIG_FILE_PATH, "r");
    if (!configFile) {
        Serial.println(F("FAIL"));
        Serial.println(F("ERROR: Unable to open config file. Using default config."));
        return;
    }

    size_t size = configFile.size();
    uint16_t freeMem = ESP.getMaxFreeBlockSize() - 512;
    if (size > freeMem) {
        Serial.println(F("FAIL"));
        Serial.print(F("ERROR: Not enough free memory to load document. Size = "));
        Serial.print(size);
        Serial.print(F(", Free = "));
        Serial.println(freeMem);
        configFile.close();
        return;
    }

    DynamicJsonDocument doc(freeMem);
    DeserializationError error = deserializeJson(doc, configFile);
    if (error) {
        Serial.println(F("FAIL"));
        Serial.println(F("ERROR: Failed to parse config file to JSON. Using default config."));
        configFile.close();
        return;
    }

    doc.shrinkToFit();
    configFile.close();

    String chipId = String(ESP.getChipId(), HEX);
    String defHostname = String(DEVICE_NAME) + "_" + chipId;

    config.hostname = doc.containsKey("hostname") ? doc["hostname"].as<String>() : defHostname;
    config.useDhcp = doc.containsKey("isDhcp") ? doc["isDhcp"].as<bool>() : false;

    if (doc.containsKey("ip")) {
        if (!config.ip.fromString(doc["ip"].as<String>())) {
            printWarningAndContinue(F("WARN: Invalid IP in configuration. Falling back to factory default."));
        }
    }
    else {
        config.ip = defaultIp;
    }

    if (doc.containsKey("gateway")) {
        if (!config.gw.fromString(doc["gateway"].as<String>())) {
            printWarningAndContinue(F("WARN: Invalid gateway in configuration. Falling back to factory default."));
        }
    }
    else {
        config.gw = defaultGw;
    }

    if (doc.containsKey("subnetmask")) {
        if (!config.sm.fromString(doc["subnetmask"].as<String>())) {
            printWarningAndContinue(F("WARN: Invalid subnet mask in configuration. Falling back to factory default."));
        }
    }
    else {
        config.sm = defaultSm;
    }

    if (doc.containsKey("dns")) {
        if (!config.dns.fromString(doc["dns"].as<String>())) {
            printWarningAndContinue(F("WARN: Invalid DNS IP in configuration. Falling back to factory default."));
        }
    }
    else {
        config.dns = defaultDns;
    }

    config.ssid = doc.containsKey("wifiSSID") ? doc["wifiSSID"].as<String>() : DEFAULT_SSID;
    config.password = doc.containsKey("wifiPassword") ? doc["wifiPassword"].as<String>() : DEFAULT_PASSWORD;
    config.mqttBroker = doc.containsKey("mqttBroker") ? doc["mqttBroker"].as<String>() : MQTT_BROKER;
    config.mqttPort = doc.containsKey("mqttPort") ? doc["mqttPort"].as<int>() : MQTT_PORT;
    config.mqttTopicControl = doc.containsKey("mqttControlChannel") ? doc["mqttControlChannel"].as<String>() : MQTT_TOPIC_CONTROL;
    config.mqttTopicStatus = doc.containsKey("mqttStatusChannel") ? doc["mqttStatusChannel"].as<String>() : MQTT_TOPIC_STATUS;
    config.mqttUsername = doc.containsKey("mqttUsername") ? doc["mqttUsername"].as<String>() : "";
    config.mqttPassword = doc.containsKey("mqttPassword") ? doc["mqttPassword"].as<String>() : "";

    #ifdef ENABLE_OTA
        config.otaPort = doc.containsKey("otaPort") ? doc["otaPort"].as<uint16_t>() : MQTT_PORT;
        config.otaPassword = doc.containsKey("otaPassword") ? doc["otaPassword"].as<String>() : OTA_PASSWORD;
    #endif

    config.alarmDepthInches = doc.containsKey("alarmDepthInches") ? doc["alarmDepthInches"].as<uint8_t>() : ALARM_DEPTH_INCHES;
    config.pitDepth = doc.containsKey("pitDepth") ? doc["pitDepth"].as<uint8_t>() : PIT_DEPTH_INCHES;
    config.pumpActivatePercent = doc.containsKey("activatePercentFull") ? doc["activatePercentFull"].as<uint8_t>() : DEFAULT_PUMP_ACTIVATE_PERCENT;
    config.pumpDeactivatePercent = doc.containsKey("deactivatePercentFull") ? doc["deactivatePercentFull"].as<uint8_t>() : DEFAULT_PUMP_DEACTIVATE_PERCENT; 

    doc.clear();
    Serial.println(F("DONE"));
}

/**
 * Confirms with the user that they wish to do a factory restore. If so, then
 * clears the current configuration file in SPIFFS, then reboots. Upon reboot,
 * a new config file will be generated with default values.
 * @param fromSubmit Set true if request came from the configuration page.
 * Default is false.
 */
void doFactoryRestore(bool fromSubmit = false) {
    String str = "N";
    if (!fromSubmit) {
        Serial.println();
        Serial.println(F("Are you sure you wish to restore to factory default? (Y/n)?"));
        Console.waitForUserInput();
        str = Console.getInputString();
    }
    
    if (str == "Y" || str == "y" || fromSubmit) {
        Serial.print(F("INFO: Clearing current config... "));
        if (filesystemMounted) {
            if (SPIFFS.remove(CONFIG_FILE_PATH)) {
                Serial.println(F("DONE"));
                Serial.print(F("INFO: Removed file: "));
                Serial.println(CONFIG_FILE_PATH);

                Serial.print(F("INFO: Rebooting in "));
                for (uint8_t i = 5; i >= 1; i--) {
                    Serial.print(i);
                    Serial.print(F(" "));
                    delay(1000);
                }

                reboot();
            }
            else {
                Serial.println(F("FAIL"));
                Serial.println(F("ERROR: Failed to delete configuration file."));
            }
        }
        else {
            Serial.println(F("FAIL"));
            Serial.println(F("ERROR: Filesystem not mounted."));
        }
    }

    Serial.println();
}

/**
 * Attempts to re-connect to the MQTT broker if then connection is
 * currently broken.
 * @return true if a connection to the MQTT broker is either already
 * established, or was successfully re-established; Otherwise, false.
 * If the connection is re-established, then will also re-subscribe to
 * the status channel.
 */
bool reconnectMqttClient() {
    if (!mqttClient.connected()) {
        Serial.print(F("INFO: Attempting to establish MQTT connection to "));
        Serial.print(config.mqttBroker);
        Serial.print(F(" on port: "));
        Serial.print(config.mqttPort);
        Serial.println(F("..."));

        bool didConnect = false;
        if (config.mqttUsername.length() > 0 && config.mqttPassword.length() > 0) {
            didConnect = mqttClient.connect(config.hostname.c_str(), config.mqttUsername.c_str(), config.mqttPassword.c_str());
        }
        else {
            didConnect = mqttClient.connect(config.hostname.c_str());
        }

        if (didConnect) {
            Serial.print(F("INFO: Subscribing to channel: "));
            Serial.println(config.mqttTopicControl);
            mqttClient.subscribe(config.mqttTopicControl.c_str());

            Serial.print(F("INFO: Publishing to channel: "));
            Serial.println(config.mqttTopicStatus);
        }
        else {
            String failReason = TelemetryHelper::getMqttStateDesc(mqttClient.state());
            Serial.print(F("ERROR: Failed to connect to MQTT broker: "));
            Serial.println(failReason);
            return false;
        }
    }

    return true;
}

/**
 * Callback method for checking the MQTT connection state and
 * reconnecting if necessary. If the connection is broken, and
 * reconnection fails, another attempt will be made after CHECK_MQTT_INTERVAL.
 */
void onCheckMqtt() {
    Serial.println(F("INFO: Checking MQTT connection status..."));
    if (reconnectMqttClient()) {
        Serial.println(F("INFO: Successfully reconnected to MQTT broker."));
        publishSystemState();
    }
    else {
        Serial.println(F("ERROR: MQTT connection lost and reconnect failed."));
        Serial.print(F("INFO: Retrying connection in "));
        Serial.print(CHECK_MQTT_INTERVAL % 1000);
        Serial.println(F(" seconds."));
    }
}
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
void loop() {
    ESPCrashMonitor.iAmAlive();
    Console.checkInterrupt();
    taskMan.execute();
    #ifdef ENABLE_MDNS
        mdns.update();
    #endif
    #ifdef ENABLE_OTA
        ArduinoOTA.handle();
    #endif
    mqttClient.loop();
}

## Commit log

2019-09-05 First version. Beta release.
    [CySump.fzz]
2019-10-28 Update board design and make depth configurable
    [CySump.fzz]
2019-11-07 Adding gerber files
    [CySump_contour.gm1, CySump_copperBottom.gbl, CySump_copperTop.gtl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]
2019-11-12 Change holes to 3mm and add text
    [CySump.fzz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]
2019-11-13 Minor update and re-export to gerber
    [CySump.fzz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]
2020-03-02 Modify sensor to use 3.3V and cleanup PCB traces
    [CySump.fzz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]
2020-04-08 Make TLS optional. Implement CLI lib. Add WL graph
    [CySump.fzz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]
2020-07-27 Switch to eTape sensor. R1.5 HW. V1.4 FW.
    [CySump.fzz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]
2020-07-28 Fixing some stupid glaring errors
    [main.cpp]
